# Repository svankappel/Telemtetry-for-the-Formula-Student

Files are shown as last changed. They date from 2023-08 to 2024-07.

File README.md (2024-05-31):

# Telemetry for the Formula Student
## Telemetry
Telemetry is a technology that enables remote measurement and monitoring.This technology is interesting for a race vehicle as it allows live readings from the car's sensors to be monitored directly from the side of the track. With such a system, the data from all the sensors are easily accessible, and the engineers can adjust the car's parameters during the test sessions to increase the car's performance. A telemetry system is also helpful in improving the driver's skills, providing measurements such as GPS, speed, pedal level, steering angle, etc. Direct visualization of measurements also allows problems to be identified before they can cause an accident or damage the car.
## Bachelor's Project
This project aimed to develop and test a telemetry system for the Formula Student car of the HES-SO Valais-Wallis. This thesis deals with the embedded part of the system and the communication with the remote PC. This project was carried out in collaboration with a Business Information Technology student working on the software to display the telemetry system's data.
## MSE PA - Optimizations
This project aimed to enhance the existing system by incorporating additional functionalities
and improving its performance. The objectives of the project are as follows :
- **Addition of a Configurable Filter for the CAN Bus:** The objective of this
section is to implement a filter on the CAN input to allow the passage of other
messages without compromising the performance of the telemetry system.
- **Telemetry System Control via CAN Bus:**
 Currently, recording is initiated and
stopped using a button connected to the system. The objective of this section
is to add the capability to control these functions via the CAN bus.
- **Integration of Time and Date:** The objective of this section is to replace the
current timestamp (relative time since recording started) with absolute time.
- **System Optimization to Enable the Recording of More Data at a Higher
Frequency:** The goal of this section is to push the limits of the number of CAN
messages the system can handle and increase the recording frequency on the SD
card.

The first two points will be implemented on the existing hardware. This is because
the VRT team will need these modifications for the summer 2024 races, and these
optimisations do not require new hardware. For the last two points, the same hardware
is reused, but it is duplicated in order to have one device for the transmission and the
other for the recording.
## Project summary
The telemetry device is connected to the sensors on the car's CAN bus. The
device also includes a GPS module. The CAN bus and GPS module data are
transmitted to the base station via Wi-Fi. The data are also saved on an SD card.
The system is designed to be generic and completely configurable. New sensors
can easily be added to the system by only changing the configuration file.
The device has been successfully developed and tested, and all the objectives
have been reached. The tests showed that the system can transmit data over a
750 meters distance.
## Git Content
The realease branch contains the project's outcome.

- The software folder contains the code of the nRF5340, the busmaster scirpts used for the tests and a configuration file example. The telemetry_system folder contains the code for the system using one device. The telemetry_system_recorder contains the code of the recoridng device for the splitted system and the telemetry_system_transmitter contains the code of the transmitting device for the splitted system. 

- The hardware folder contains the Altium projects, the Bill of material and the Fusion 360 file for the antenna holder.
- The Report folder contains the report of the project. 
- The Miscellaneous folder contains an example of the configuration file, a test and measurement file etc...

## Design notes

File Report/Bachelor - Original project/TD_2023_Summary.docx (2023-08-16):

Telemetry for the Formula Student

| Graduate Sylvestre van Kappel

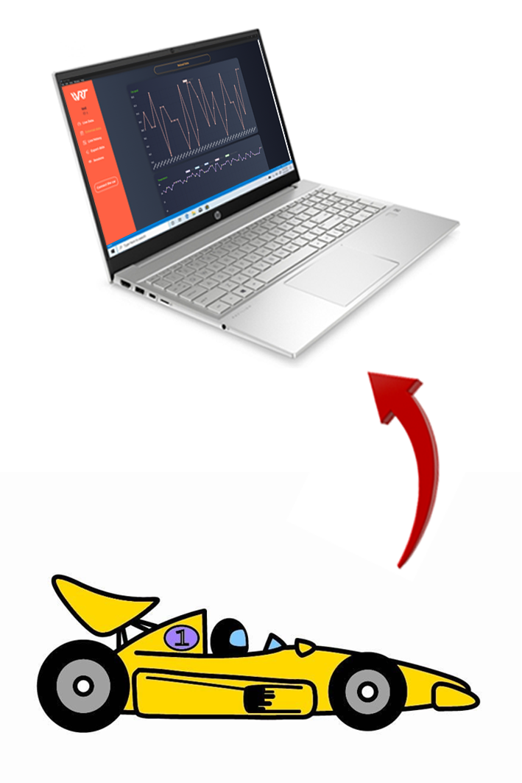
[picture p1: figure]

Bachelor’s Thesis
| 2023 |

Degree programme

Systems Engineering

Field of application

Infotronics

Supervising professor

Medard Rieder

medard.rieder@hes-so.ch

Partner

Valais-Wallis Racing Team

Objectives

This project aims to develop and test a telemetry system for the Formula Student car of the HES-SO Valais-Wallis. This thesis deals with the telemetry system's onboard device and the communication with the PC.

Methods | Experiences | Results

Telemetry is a technology that enables remote measurement and monitoring. This technology is interesting for a race vehicle as it allows live readings from the car's sensors to be monitored directly from the side of the track. With such a system, the data from all the sensors are easily accessible, and the engineers can adjust the car's parameters during the test sessions to increase the car's performance.

The objective of this project is to select the optimum transmission technology and to design and test the hard- and software of the telemetry system’s onboard device.

The telemetry device is connected to the sensors on the car's CAN bus. The device also includes a GPS module. The CAN bus and GPS module data are transmitted to the base station via Wi-Fi. The data are also saved on an SD card. The system is designed to be generic and completely configurable. New sensors can easily be added to the system by only changing the configuration file.

The device has been successfully developed and tested, and all the objectives have been reached. The tests showed that the system can transmit data over a 750 meters distance.

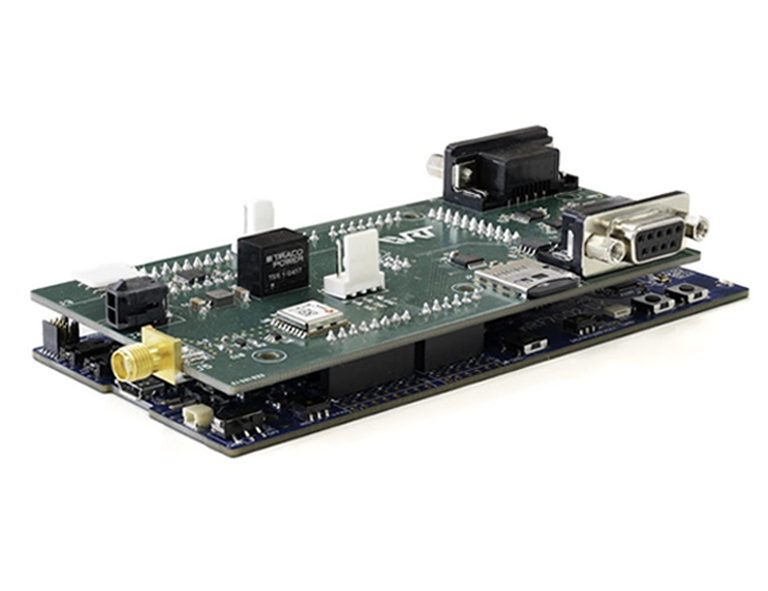
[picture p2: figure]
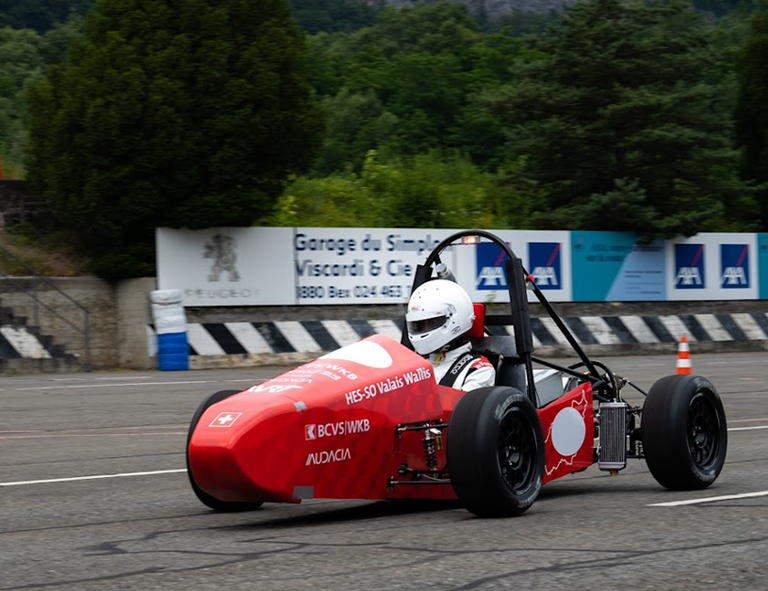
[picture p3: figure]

Valais-Wallis Racing Team’s Car

Telemetry onboard device

HES-SO Valais-Wallis • rue de l’Industrie 23 • 1950 Sion +41 58 606 85 23 • hei@hevs.ch • www.hevs.ch/hei

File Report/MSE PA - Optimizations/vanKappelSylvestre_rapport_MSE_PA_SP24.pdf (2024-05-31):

i

Master of Science HES-SO in Engineering
Av. de Provence 6

# CH-1007 Lausanne Master of Science HES-SO in Engineering

# Major : Computer Science (CS)

# Telemetry for the Formula Student -Optimizations

By

# Sylvestre van Kappel

## Under the supervision of Prof. Medard Rieder HES-SO Valais Wallis

## Sion, HES-SO//Valais-Wallis, 31.05.2024

### Accepted by the HES SO//Master (Switzerland, Lausanne) on the proposal of

### Prof. Medard Rieder, supervisor for the in-depth project

### Sion, 31.05.2024

### Prof. Medard Rieder Supervisor

### Prof. Nabil Abdennadher Program director

# Contents

Contents | iv
List of Figures | vi
List of Tables | vi
List of Listings | vi
1 Introduction | 1
2 System Overview | 5
3 Hardware | 9
4 Software Development | 13
5 Tests | 31
6 Conclusions | 35

iv/41

Contents

7 Appendix | 37
Bibliography | 39
Acronyms | 41

v/41

# List of Figures

1.1 | Valais-Wallis Racing Team’s Car | | 1
1.2 | Current Hardware | | 3
2.1 | System Overview | | 5
2.2 | Telemetry System Display | | 7
3.1 | Bloc Diagram - Current System | | 9
3.2 | Bloc Diagram - New System | | 10
3.3 | New Hardware | | 11
4.1 | Data-Flow Diagram | | 14
4.2 | CAN Button Sequence | | 17
4.3 | GPS Time and Date Data Sequence | | 19
4.4 | CAN Data Sequence | | 21
4.5 | Recording Device Flow Diagram | | 22
4.6 | Transmitting Device Flow Diagram | | 23
4.7 | Booting Sequence | | 24
4.8 | Configuration Transmission | | 25
4.9 | Configuration Reception | | 26
4.10 GPS CAN Frames | | 27
4.11 GPS CAN Frames Transmission | | 28
4.12 GPS CAN Frames Reception | | 29
5.1 | Limits of the system - Base system and upgrades on the existing hardware 32
5.2 | Limits of the system - Base system, upgrades on the existing hardware
| and new hardware | | 33
5.3 | Limits of the system - New System | | 34

# List of Tables

4.1 | CSV File Structure | | 18

vi/41

List of Listings

# List of Listings

4.1 | Configuration of the CAN filter | | 15
4.2 | Configuration of the Record-on-Start | | 16
4.3 | Configuration of the CAN Button | | 16
4.4 | Configuration of the CAN Button | | 17
4.5 | Configuration of the CAN Button | | 27

vii/41

# 1 | Introduction

## 1.1 Formula Student

Formula Student is an international student engineering competition. Teams from all over the world design and build a small-scale Formula-style racing car. During the competitions, the vehicles are judged on static events: Engineering Design, Cost and Manufacturing, Business Presentation, Lap Time Simulation, and Technical Inspection. The vehicle must comply with the rules [1] for the technical inspection. If the car passes the technical assessment, it can participate in the dynamic events: Skidpad, 1 km autocross/sprint, 75 m acceleration, and 22 km endurance.

## 1.2 Valais-Wallis Racing Team

The Valais-Wallis Racing team [2] is the Formula Student team of HES-SO Valais Wallis. It was founded in the spring of 2022 by a group of students. The team’s inaugural car participated in the summer 2023 races, and the telemetry system developed in this thesis will be utilized in the subsequent car for the summer 2024 races. Telemetry was not integrated into the initial car; however, a telemetry system was designed during the summer of 2023.

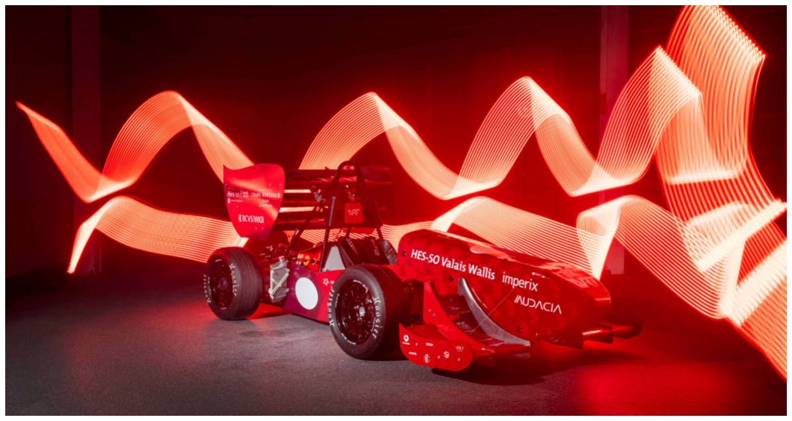
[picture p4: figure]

Figure 1.1: Valais-Wallis Racing Team’s Car

Chapter 1. Introduction

## 1.3 Objectives

Telemetry is a technology that enables remote measurement and monitoring. This technology is interesting for a race vehicle as it allows live readings from the car’s sensors to be monitored directly from the side of the track. With such a system, the data from all the sensors are easily accessible, and the engineers can adjust the car’s parameters during the test sessions to increase the car’s performance. A telemetry system is also helpful in improving the driver’s skills, providing measurements such as GPS, speed, pedal level, steering angle, etc. Direct visualization of measurements also allows problems to be identified before they cause an accident or damage to the car.

This project aims to enhance the existing system by incorporating additional functionalities and improving its performance. The objectives of the project are as follows :

- Addition of a Configurable Filter for the CAN Bus: The objective of this section is to implement a filter on the CAN input to allow the passage of other messages without compromising the performance of the telemetry system.
- Telemetry System Control via CAN Bus: Currently, recording is initiated and stopped using a button connected to the system. The objective of this section is to add the capability to control these functions via the CAN bus.
- Integration of Time and Date: The objective of this section is to replace the current timestamp (relative time since recording started) with absolute time.
- System Optimization to Enable the Recording of More Data at a Higher Frequency: The goal of this section is to push the limits of the number of CAN messages the system can handle and increase the recording frequency on the SD card.

The first two points will be implemented on the existing hardware. This is because the VRT team will need these modifications for the summer 2024 races, and these optimisations do not require new hardware. For the last two points, the same hardware is reused, but it is duplicated in order to have one device for the transmission and the other for the recording.

1.4 Structure of this Report

## 1.4 Structure of this Report

This report is in 4 parts.The first part is a general overview of the system. The second part describes the small hardware modifications that were made, and the third part describes the software optimisations. The last part describes the various tests that were carried out.

## 1.5 Git

All the files referring to the project (codes, altium PCB project ...) and the first release of the project are available on a git repository on the following link :

https://github.com/svankappel/Telemetry-for-the-Formula-Student

## 1.6 Existing Hardware

The following image shows the existing hardware :

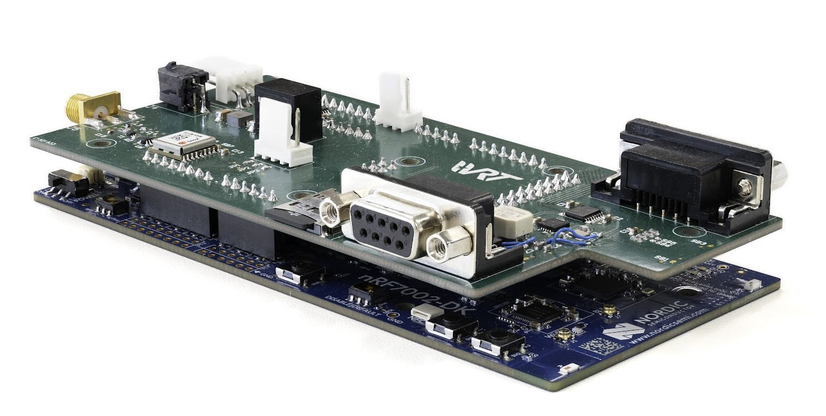
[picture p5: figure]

Figure 1.2: Current Hardware

# 2 | System Overview

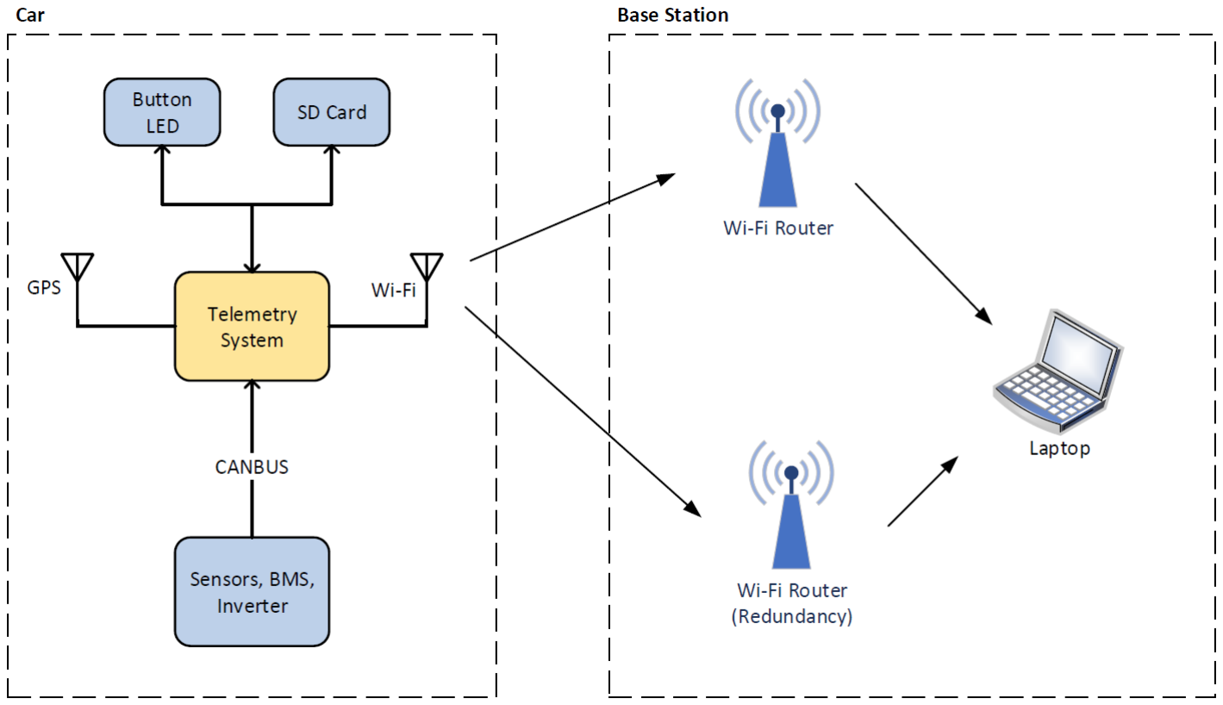
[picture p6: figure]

Figure 2.1: System Overview

This diagram shows the general functioning of the telemetry system. The data coming from the sensors are transmitted by Wi-Fi to the base station.

## 2.1 CAN Bus

The CAN bus is a widely used communication protocol in automotive applications. It was developed in the 1980s by Bosch to allow reliable communication between ECUs in vehicles. The CAN bus protocol is robust and fast. It can handle multiple devices on a single network while maintaining reliability and data integrity.

The CAN bus connects all the different devices of the car that need to communicate. The messages contain various parameters, such as engine speed, pedal status, temperature of the different components, etc. The BMS and the inverter in the actual car include a CAN interface. These two components provide some measurements such as voltage and current of the High Voltage system, power, temperatures, and angular speed. The car will also include more sensors also connected to the CAN bus.

The telemetry system is connected to the CAN bus and retransmits the data from the sensors.

Chapter 2. System Overview

## 2.2 SD Card

The system includes an SD card. The SD card has two functions.

The first function is to hold a configuration file. It is a JSON file that contains all the information the system needs to work correctly. The configuration file contains the settings for every sensor. A new sensor can be easily added by putting its CAN settings in the configuration file.

The second function is to register the measurements made by the sensors. When the button is pressed, the recording is activated, and the LED on the button blinks. When the button is pressed again, the recording is stopped. The data on the SD card provide a backup in case the transmission is interrupted. The data from all sensors are recorded at a high frequency. These data are saved in CSV files.

## 2.3 Wi-Fi Transmission

The Wi-Fi transmission includes an optional redundancy. When it is activated, the system tries to connect to the first router. If it cannot connect, it tries with the second router. It then retries with the first if the second is unreachable, etc.

The settings of the Wi-Fi connection (SSID, password) are set in the configuration file. The system can use any standard Wi-Fi router. It employs the WPA2 security protocol but can be easily migrated to WPA3.

The data of only a selected number of sensors shall be live transmitted to the base station. A boolean field in the configuration file indicates whether the data of each sensor shall be transmitted or not. The transmission frequency is also defined in the configuration file. The defined frequency is lower than the recording frequency.

## 2.4 GPS

The telemetry device includes a GPS. It provides the GPS coordinates and the speed of the car. As for the sensors, the data are saved in the CSV files and can also be sent by the Wi-Fi transmission.

2.5 Front End

## 2.5 Front End

The software on the base station’s PC displays the data sent by the telemetry device. The data saved on the SD card can also be loaded on the software. This software was developed by a student from the Business Information Technology program.

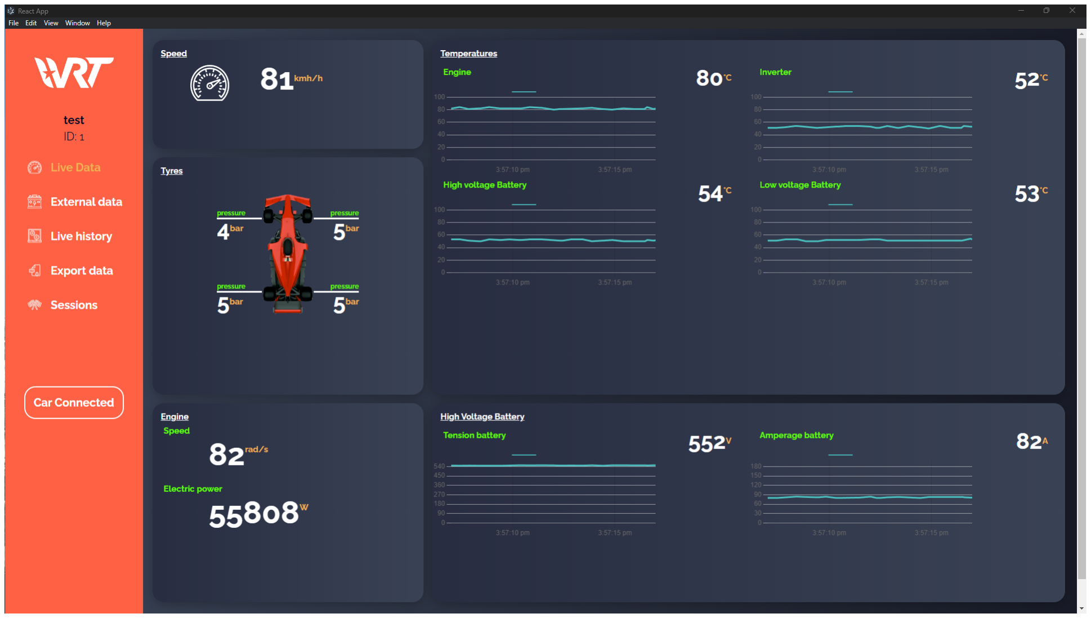
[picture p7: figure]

Figure 2.2: Telemetry System Display

The software can be downloaded at the following link :

https://vrt.simonbeaud.ch/

## 2.6 Optimizations

The optimizations do not alter the general system overview. The system continues to function in the same manner. The CAN filter and CAN button functionalities merely introduce some configuration adjustments in the configuration file. The inclusion of time and date provides additional data in the CSV recording file.

# 3 | Hardware

## 3.1 Existing System

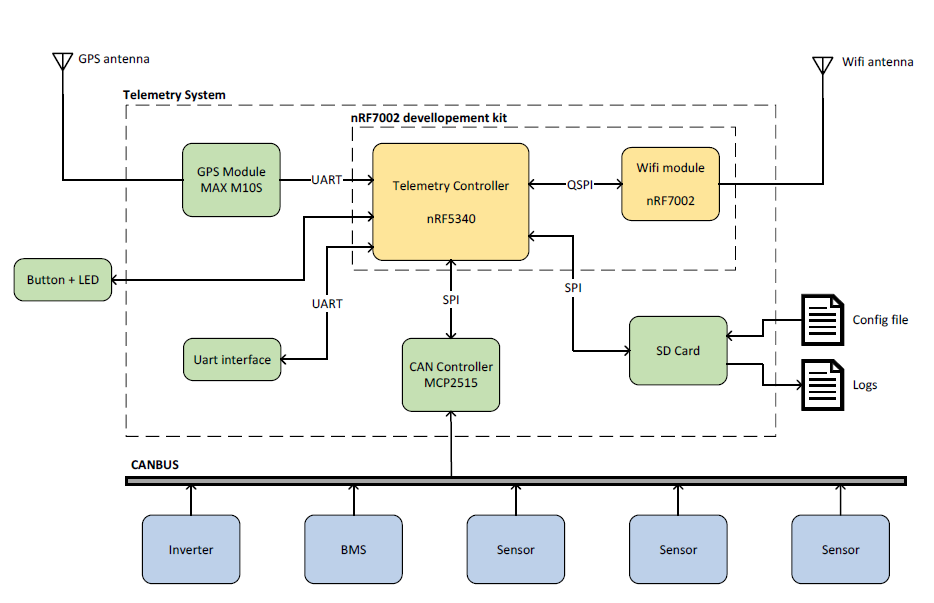
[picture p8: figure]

Figure 3.1: Bloc Diagram - Current System

This diagram shows the general architecture of the telemetry system’s onboard device. The CAN Filter and the CAN button are implemented on this version on the hardware (and also on the new version).

The main controller (nRF5340) is the central element of the system.

The CAN controller is connected to the nRF5340 via an SPI bus. On the other side, it is connected to the CAN bus to communicate with the BMS, the inverter, and all the sensors.

Another peripheral is the GPS module. It is connected to the nRF5340 via a UART communication. The GPS module uses an external antenna because it needs to be pointed to the sky, and the telemetry system will be placed in a case in the car.

The microSD card is connected to the nRF5340 via an SPI bus. The microSD card serves to store the measurements of the telemetry system. The memory card also holds a configuration file.

The nRF7002 chip handles Wi-Fi communication. It is connected to the nRF5340 via a QSPI bus. As for the GPS module, the Wi-Fi module uses an external antenna to improve the transmission.

Chapter 3. Hardware

The system also includes a button with an intern LED. The button permits to start and stop the recording of the logs, and the LED indicates the system’s status. The button will be placed on the dashboard of the car.

The last peripheral is a UART interface. The telemetry system does not use it. It is just there for future system improvements (to connect an onboard computer, for example).

## 3.2 New System

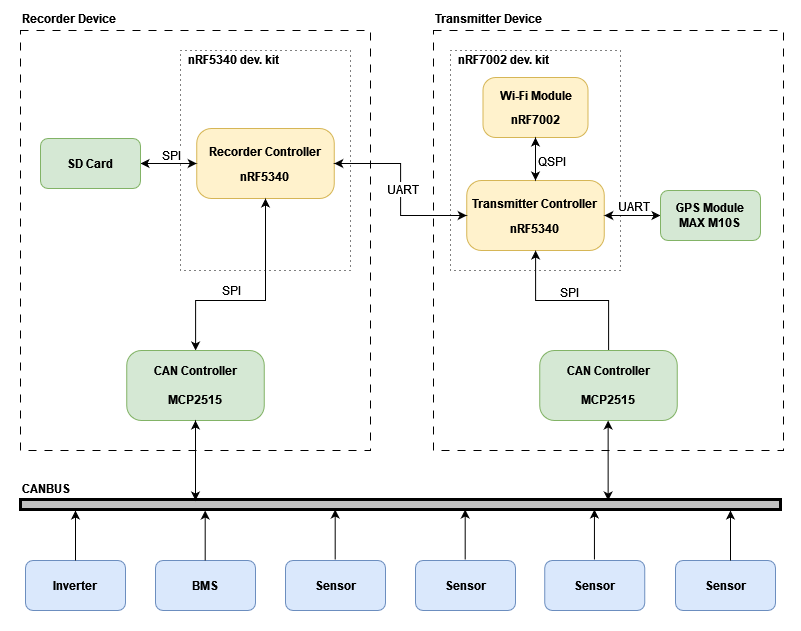
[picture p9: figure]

Figure 3.2: Bloc Diagram - New System

The new hardware is identical to the existing version, but the system has been duplicated, with only the components required by each respective device being mounted on the PCB. For the recording device, the nRF7002DK was replaced by a nRF5340DK as it does not require Wi-Fi. The two devices are connected together via a UART bus and they both have their own CAN Controller.

3.2 New System

The following image shows the new hardware:

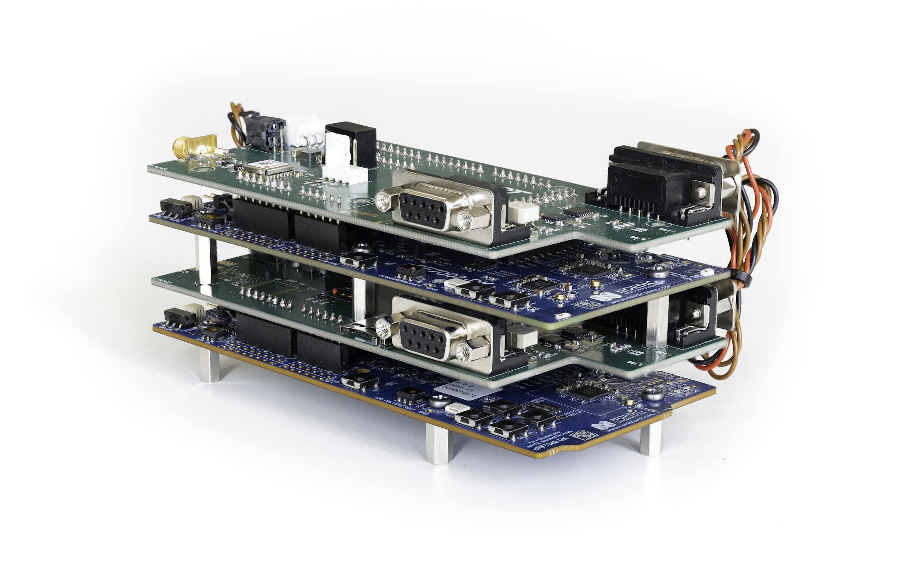
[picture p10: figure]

Figure 3.3: New Hardware

# 4 | Software Development

## 4.1 Existing System Design

The software implemented on the nRF5340 uses the Zephyr RTOS. Zephyr RTOS is a compact operating system designed for devices with limited resources. Nordic’s advanced hardware, renowned for its performance and efficiency, fits absolutely with Zephyr’s lightweight and modular design.

The software is implemented on the application processor of the nRF5340. It was developed with the nRF Connect SDK v2.3.0.

The software implements the following tasks working in parallel:

- Wi-Fi Station
- UDP Client
- Data Sender
- Data Logger
- GPS Controller
- CAN Controller
- Button Manager
- LED Controller

The main function starts the Button Manager and the LED Controller first. Then the configuration file is read, and all the other tasks are started if the reading of the file is successful.

The design includes two buffers. The first is the sensor buffer. It contains the value and the configuration of every sensor present in the configuration file. The CAN Controller writes the values received by the sensors on this buffer. The second buffer is the GPS buffer. It works like the sensor buffer but takes its data from the GPS Controller.

The Data Sender periodically reads the sensor and GPS buffers and creates a JSON message containing the sensor and GPS values configured to be sent on the live transmission. Then it puts it in the UDP queue.

The UDP Client reads the UDP queue and sends the messages to the base station via the Wi-Fi using a UDP socket. The UDP protocol was chosen because it is faster than TCP, and the transmission does not need to be 100% reliable because the messages are periodically re-transmitted. Consequently, it is not a problem if sometimes a transmission contains an error.

When the button is pressed, the Data Logger creates a new CSV file on the SD card. It then periodically reads the sensor and GPS buffers and writes a new line on the CSV file with the read values. When the button is pressed again, the recording is stopped. The LED on the button is blinking when the Data Logger is recording.

The Wi-Fi Station manages the Wi-Fi connection.

Chapter 4. Software Development

The following diagram shows the system’s general architecture:

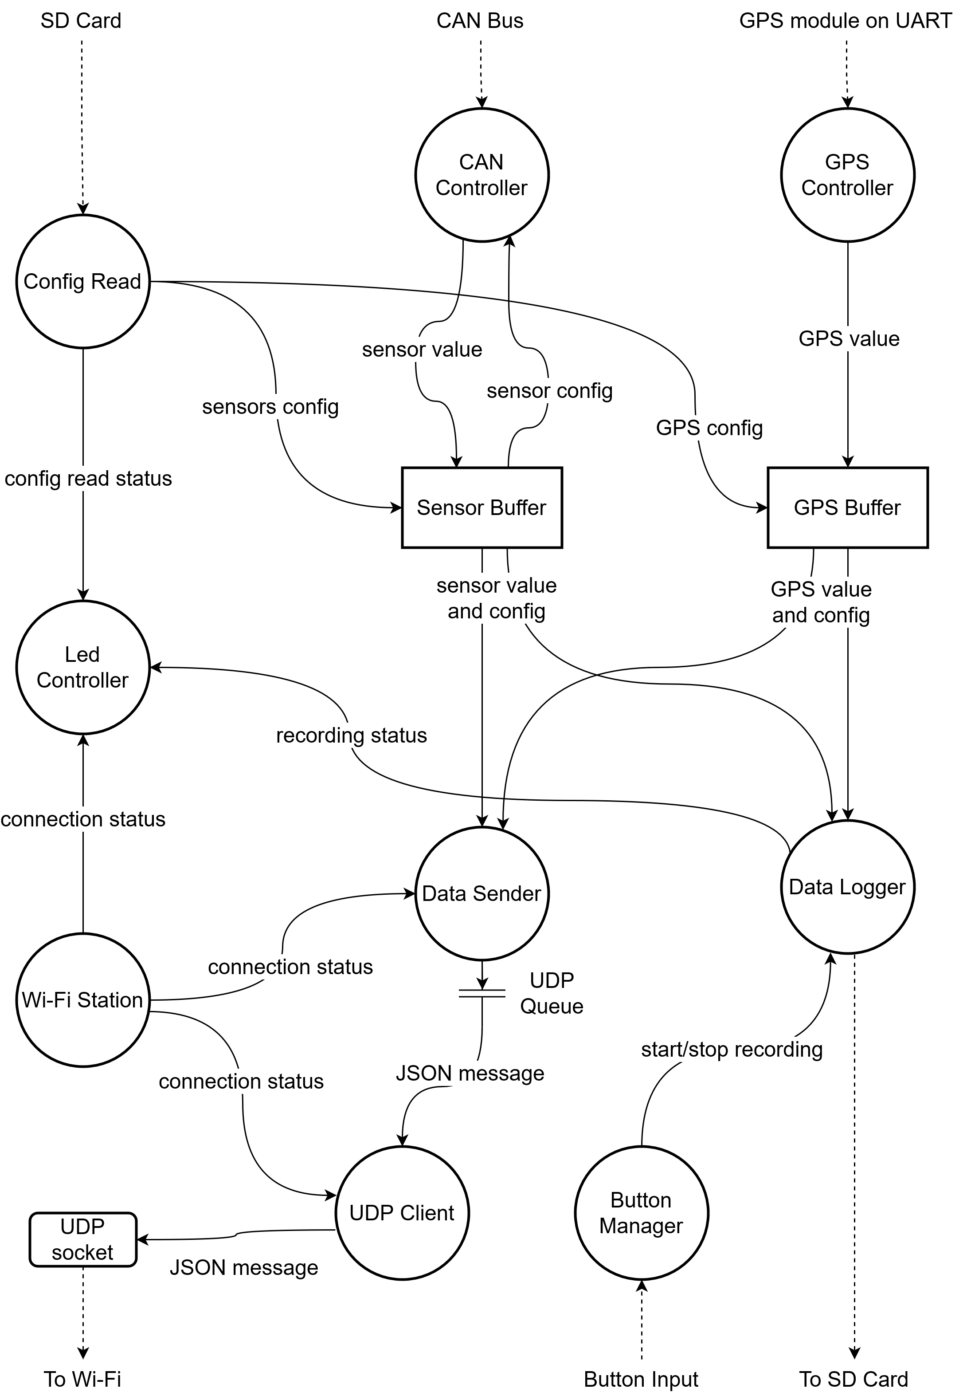
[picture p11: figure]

Figure 4.1: Data-Flow Diagram

4.2 CAN Filter

## 4.2 CAN Filter

The first optimization added to the system is the CAN filter. The Zephyr CANBUS API
[3] allows a CAN filter to be set. Messages not intended for the telemetry system are also sent over the CANBUS. The existing system also processes these messages, reads them, and then ignores them. This takes some time and affects the performance of the system. Tests have shown that the system cannot handle more than 200 messages per second to function reliably. By adding a CAN filter, a range can be defined, and message IDs that are not in the range will be ignored without affecting the performance of the system.

The CAN filter is set during the initialization of the CAN device in the CAN controller component. It takes two arguments: an ID and a mask. The filter works as follows:

A message is accepted if the following condition is true :

(filter ID & mask) == (message CAN ID & mask)

For instance, with the following configuration, only messages with a CAN ID in the specified range will be considered:

ID = 0xAA = 0b10101010

Mask = 0xF0 = 0b11110000

Messages taken into consideration are 0xA0, 0xA1, ..., 0xAF.

This allows creating ranges of CAN IDs that are designated for the telemetry system.

As the system must be configurable, the ID and mask have been added to the configuration file of the system. The configuration file is read when the program starts, and the values are stored in a structure that is then accessed by all the components of the system.

"CANFilter":
{
"id":"0x0",
"mask":"0x0"
}

Listing 4.1: Configuration of the CAN filter

Chapter 4. Software Development

## 4.3 CAN Button

On the existing system, the only way to start and stop the recording is to push the physical button. An LED on the button indicates if the system is currently recording.

The goal of this part is to start and stop the recording with a message on the CAN bus. The telemetry system must also emit a message on the CANBUS to indicate if it is currently recording or not, to replace the LED. This allows the button and the LED to be connected via the CANBUS, avoiding additional wiring. With this solution, the telemetry system will also be controllable by the on-board computer. The system must also include an option to automatically start the recording on boot.

To achieve this, several configurations have been added to the configuration file. The first is a boolean to enable recording on startup:

"RecordOnStart":false,

Listing 4.2: Configuration of the Record-on-Start

Next, there are the button configurations. There are two configurations: one to start and one to stop the recording. These configurations require a CAN ID, the length of the message, the index of the byte that contains the information in the message, the match value (the value the message must correspond to in order to start/stop the recording), and finally a mask for this match, which allows using only a single bit so the same byte can transmit other information:

"CANButton":
{
"StartLog":
{
"CanID":"0x010",
"dlc":8,
"index":7,
"match":"0x01",
"mask":"0x01"
},
"StopLog":
{
"CanID":"0x010",
"dlc":8,
"index":7,
"match":"0x00",
"mask":"0x01"
}
},

Listing 4.3: Configuration of the CAN Button

4.3 CAN Button

There is also a configuration for the "LED". A message indicates if the device is recording. For this, the system will emit a 0x01 when it is recording and a 0x00 when it is not recording, on the CAN ID specified in the configuration:

"CANLed":
{
"CanID":"0x11"
},

Listing 4.4: Configuration of the CAN Button

To send the LED message, an event was added to the Data Logger component. When the recording successfully starts, a function is called in the CAN Controller. A callback method with a function pointer is used to pass the functions to the Data Logger. In the CAN Controller, the message is formed with the CAN ID configured in the configuration file, and the message is sent.

For the CAN Button, when a message arrives on the CAN, it is put in a queue that the CAN Controller component reads. If the CAN ID matches the ID of the start or stop message, the same function that is called by the button controller is invoked. This creates a work item [4] that then calls the start or stop function in the Data Logger component.

The following diagram shows the sequence of the function called when a start message arrives on the CANBUS :

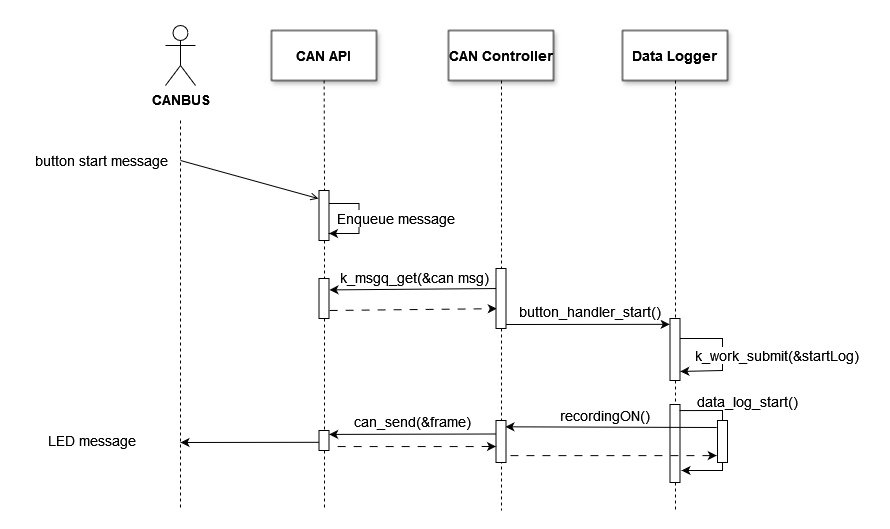
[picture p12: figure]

Figure 4.2: CAN Button Sequence

Chapter 4. Software Development

## 4.4 Time and Date

The aim of this chapter is to add a time and a date to the recordings. For this, the system needs to know the current time. There are three options to achieve this:

- Remote PC: The first option is to request the time from the remote PC via Wi-Fi communication. The issue with this approach is that the system may be used without Wi-Fi, in which case it would not be able to provide the time.
- Real-Time Clock (RTC): An RTC is an integrated circuit that provides the time. It must be powered by a small battery to retain the time when the system is powered off. The drawback is that hardware modifications would be necessary, and there was not enough time for such modifications in this project.
- GPS: The system’s GPS module also provides the time and date. The only problem is that the GPS signal can be weak indoors. To ensure this would not cause problems, tests were conducted in the Valais-Wallis Racing Team’s workshop. The results indicated that the GPS signal inside the workshop was strong enough to obtain the time and position as quickly as outside.

The GPS module works with the NMEA protocol [5]. Frames are transmitted to the nRF5340 via a UART bus. The frame that contains the date and time is the RMC frame. The GPS module sends data every second. On reception, it triggers an interrupt. During the interrupt routine, the message is pushed to a queue. The GPS Controller component reads from the queue, parses the NMEA frame, and writes the time and date data to the GPS buffer. When a recording is started in the Datalogger component, the time and date are read on the GPS buffer and written to the first line of the CSV file.

The CSV file uses the following structure:

Date: | 31-05-2024 | Time: | 09:45:12
Timestamp [ms] | Sensor1 | Sensor2 | Sensor3 | Sensor4
50 | 10 | 34567 | 156 | 332
100 | 12 | 30678 | 876 | 333
150 | 15 | 22344 | 459 | 335

Table 4.1: CSV File Structure

4.4 Time and Date

The following diagram show the sequence of the GPS data from the GPS module to the CSV file:

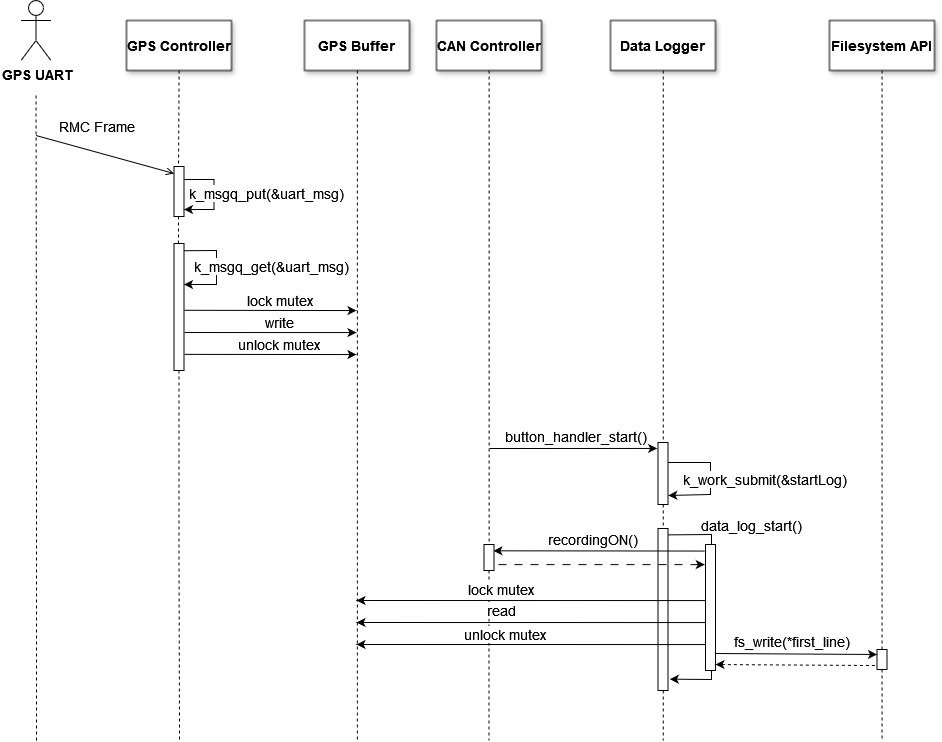
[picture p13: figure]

Figure 4.3: GPS Time and Date Data Sequence

Chapter 4. Software Development

## 4.5 System Optimization

The aim of this chapter is to optimise the performance of the system. Currently the system can process 200 messages per second on the CAN bus. If the message rate exceeds this limit, data loss can occur because the processor does not have enough time to process each message and write the data to the SD card. In addition, the processor must simultaneously handle Wi-Fi connectivity, data transfer and GPS tasks. These parallel operations fully utilise the processor’s capacity, resulting in incoming CAN messages arriving faster than they can be processed. To prevent data loss, the CAN controller uses a FIFO buffer to temporarily store messages until they are processed. However, if the buffer fills up faster than it can be emptied, any further incoming data will be lost once the buffer is full.

It’s important to note that the 200 messages per second limit may vary depending on other system configurations, such as the frequency of writing to the SD card and the amount of data written to the SD card. These factors have a significant impact on overall system performance and its ability to handle incoming messages without data loss.

There are two ways to optimise the performance of the system. The first is to reduce the time taken by tasks that are frequently called, and the second is to reduce the number of tasks that are executed by the processor by splitting the system between two processors. The split was made so that one processor was dedicated to recording on the SD card and the other to transferring the data.

4.5.1 Optimization on the existing device The existing system is already relatively straightforward, with limited opportunities for optimization. The only significant non-essential time-consuming process is the periodic synchronisation of the SD card [6]. When the function to write to the SD card is called, the data is not necessarily written directly to the SD card. Instead, the data is initially written to a cache memory, which is then copied to the SD card when a significant amount of data has accumulated. In the current system, the cache is periodically flushed in order to save data in the event that the user fails to stop recording before shutting down the system. However, in the new car, the recording is controlled by the car’s embedded computer rather than a human operator. Consequently, this situation will not occur, and the periodic synchronization can be eliminated.

4.5 System Optimization

The data is written to the sd card with the following sequence:

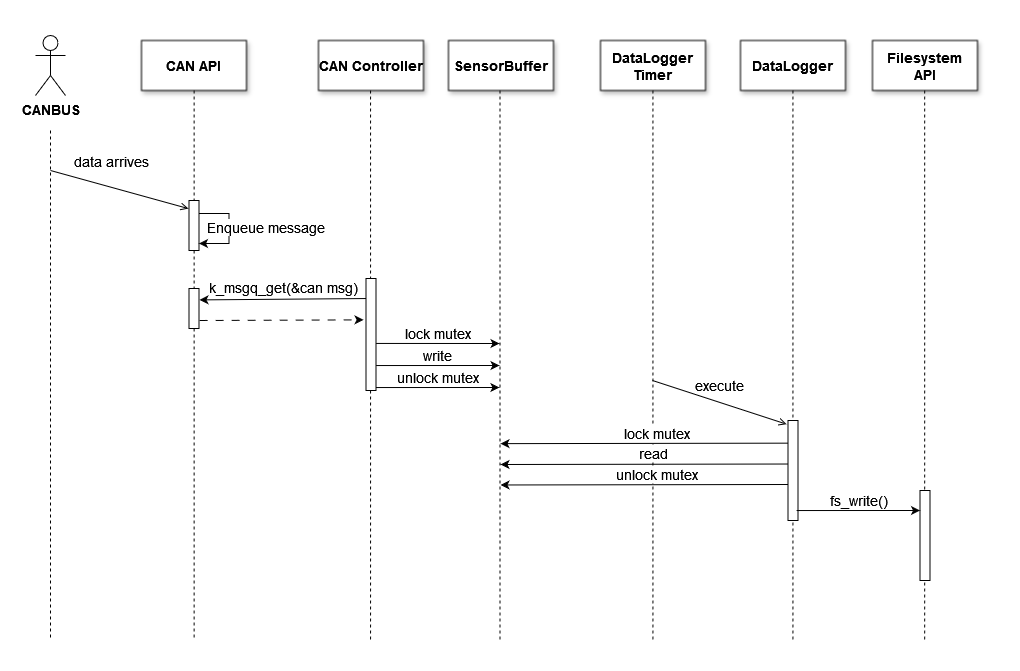
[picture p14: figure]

Figure 4.4: CAN Data Sequence

4.5.2 | Optimization on the new hardware
| To improve the optimization, the device was duplicated, with one dedicated to trans- mitting and the other to recording. This allows two factors of improvement: first, each processor has fewer tasks to manage, and second, the processor dedicated to recording can run at 128 MHz instead of 64 MHz, since Wi-Fi requires the processor to run at 64 MHz in the SDK version used during development.
| Dividing the system into two units makes it possible to eliminate certain tasks on each unit. The GPS is kept only on the transmission device, since the priority is to optimize the recording function. The SD card is kept only on the recording device. Consequently, GPS data must be transferred to the recording device and the configuration file must be transferred to the transmission device.

Chapter 4. Software Development

The following data flow diagram shows the general architecture of the recording device:

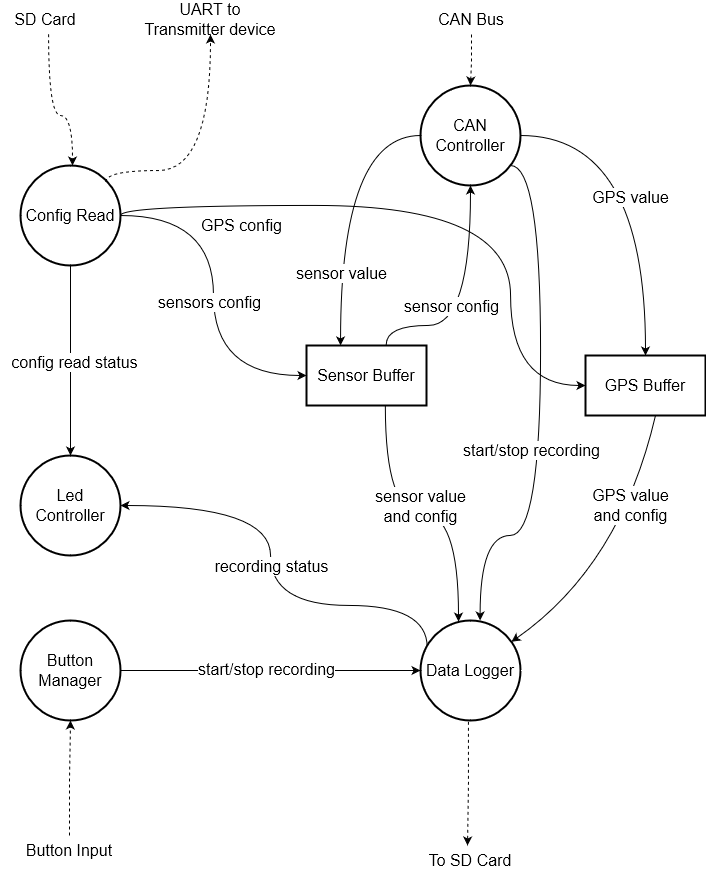
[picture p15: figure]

Figure 4.5: Recording Device Flow Diagram

4.5 System Optimization

The following data flow diagram shows the general architecture of the transmitting device:

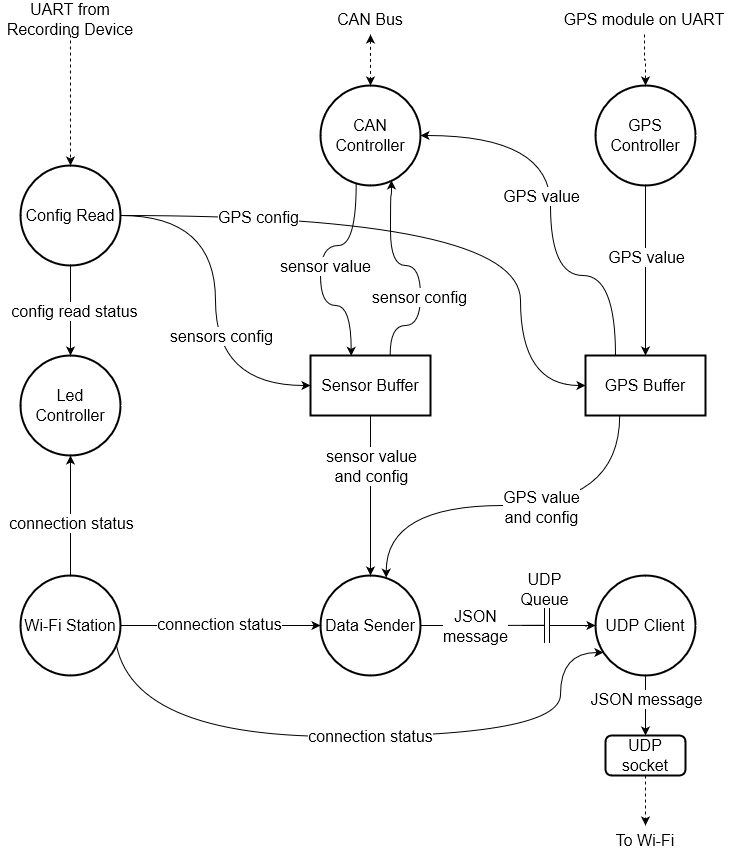
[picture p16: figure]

Figure 4.6: Transmitting Device Flow Diagram

Chapter 4. Software Development

4.5.3 Configuration File Transfer The configuration file is transferred from the recording device, which has the SD card, to the transmitting device using a UART bus. Because the file is 8 KB, this transfer is more complex than the control of the GPS module (e.g., GPS, as described in the original device report), which is only a few bytes. The transmission uses the Zephyr UART [7] with the interrupt-driven API. The UART device is configured to operate at a baud rate of 115200. At this speed, an 8 KB configuration file is transferred in approximately one second. When the system powers up, the LED and button controllers are initialized first on both devices. Next, the transmitter device pauses and waits for the configuration. On the recording device, the configuration file is read and parsed before being sent via UART. After the configuration is sent, all other components of the recording device are initialized and started. Once the transmitting device receives the configuration, it parses the file and then starts the other components. The following diagram shows the booting sequence on both devices :

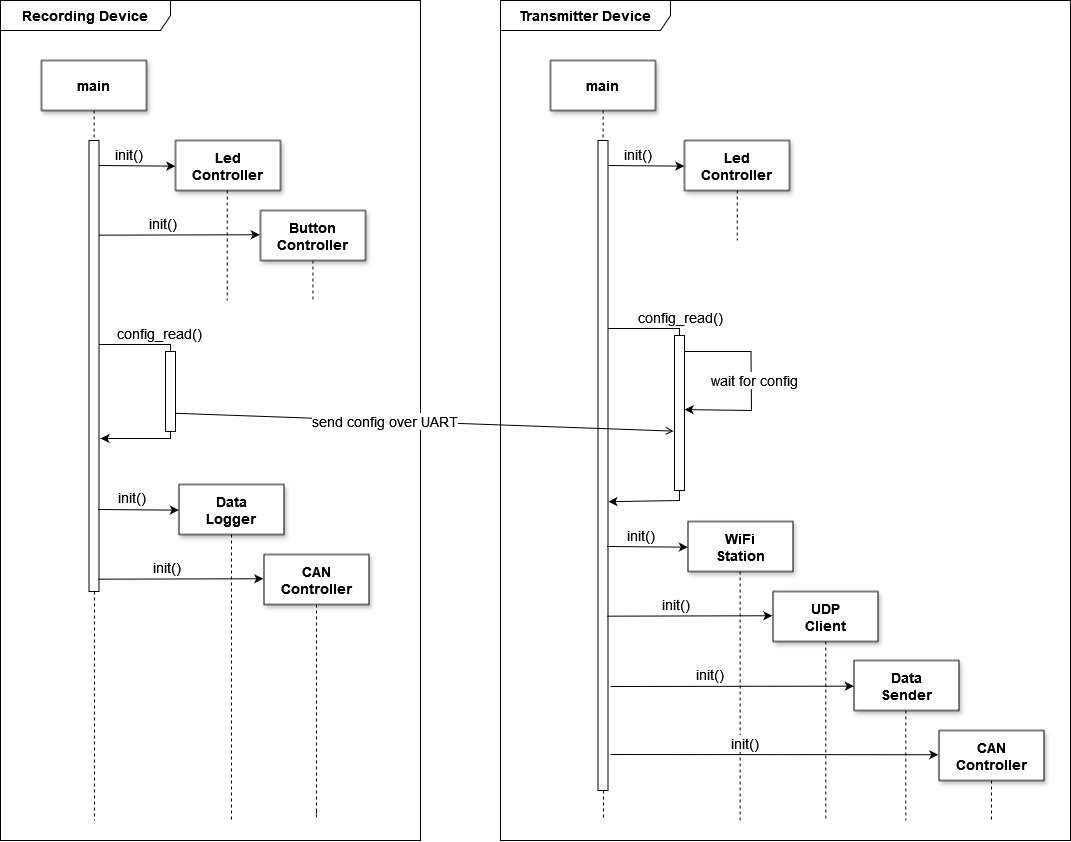
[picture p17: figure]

Figure 4.7: Booting Sequence

For the transmission of the configuration file, the code works with small temporary buffers and the bytes are copied using the memcpy operation, which copies multiple bytes simultaneously. This is important because bytes need to be stored quickly as they arrive. Copying bytes one at a time using the polling API is insufficient because the bytes arrive faster than they can be stored, resulting in data loss.

4.5 System Optimization

For the send portion, when the UART interrupt is enabled, an interruption is triggered when the device is ready to send data. During the interrupt routine, the system attempts to send a 512-byte chunk. The send function returns the number of bytes actually sent; if less than 512 bytes are sent, the system continues to send the remaining bytes in a loop. When the chunk is completely sent, the system waits for the next interruption to send the next chunk. The buffer containing the configuration file is slightly larger than the file itself and is initialized with "\0" to ensure that a terminating character is automatically added. After the entire file has been sent, the 0x14 symbol indicates that the transfer is complete. Once the file is sent, the UART device interruption is disabled as it is no longer needed.

The following activity diagram shows how the transmission works:

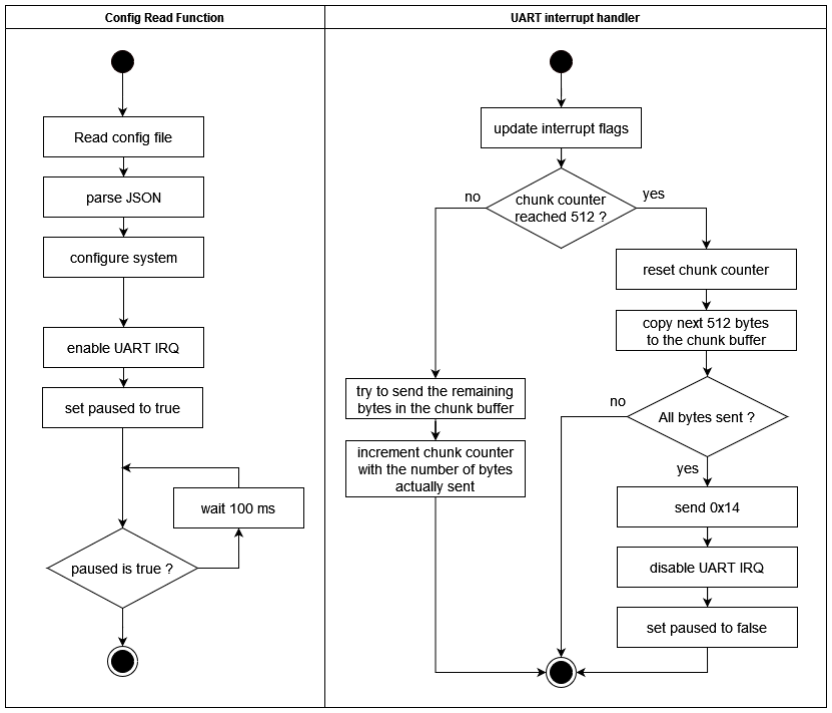
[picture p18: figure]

Figure 4.8: Configuration Transmission

A similar process applies to the receiving part. An interrupt is generated when new bytes arrive in the UART receiver. During the interruption, the system attempts to read a 64-byte chunk. The read function returns the number of bytes read, and the system copies those bytes into the buffer containing the complete configuration file. The system then waits for the next interrupt to continue copying bytes from where it last stopped. When the terminator (0x14) is detected, the UART device interrupt is disabled because it is no longer needed.

Chapter 4. Software Development

The following activity diagram shows how the reception works:

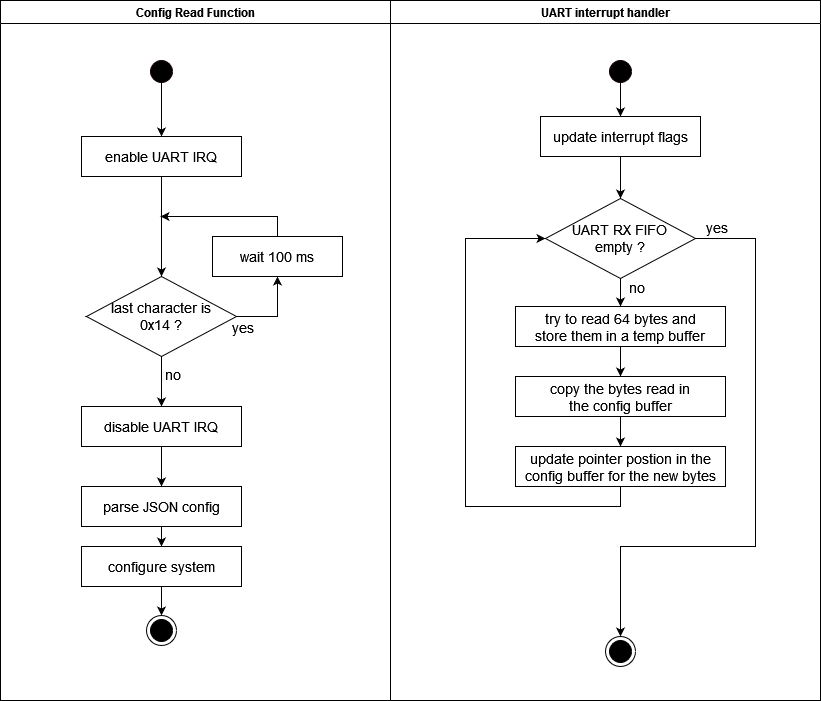
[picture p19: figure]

Figure 4.9: Configuration Reception

4.5 System Optimization

4.5.4 | GPS data transfer
| The GPS data is parsed and small calculations (e.g., unit conversions, as detailed in the original device report) are performed on the transmission device. The data is then transmitted over the CAN bus to the recording device. On the recording device, the data is placed in the GPS buffer, mimicking the input from the GPS module. Using the CAN bus allows the same thread to handle receiving data from the GPS and other sensors, improving performance.
| As data is transferred over the CAN bus, CAN IDs must be assigned to the system. To ensure the system is configurable, a field was added to the GPS section of the configuration file. Three IDs need to be assigned: the first for a message containing the longitude, the second for the latitude, and the third for a message that includes the fix information, vehicle speed, time, and date.
| The configuration file section simply contains three fields for the CAN IDs:
| "CanIDs": { "Lat":"0x05", "Long":"0x06", "TimeFixSpeed":"0x07" }
| Listing 4.5: Configuration of the CAN Button

The following figure illustrates how the data is stored in the CAN frame:

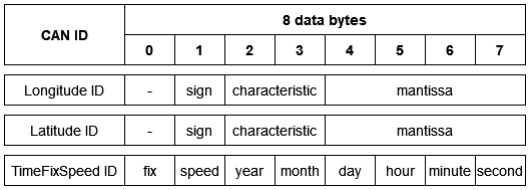
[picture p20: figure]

Figure 4.10: GPS CAN Frames

Chapter 4. Software Development

On the existing system, GPS data is received by the GPS Controller component. The data is then written to the GPS Buffer. To send the data to the recording device, a new timer was added with a period fixed at 1 second, matching the GPS module’s data transmission rate. During the timer interruption, a work item [4] is submitted to avoid blocking other processes during the interruption. In the work handler, CAN frames are created with the values currently present in the GPS buffer and are sent using the Zephyr CAN API [3].

The following sequence diagram shows how the GPS data are sent over the CAN bus:

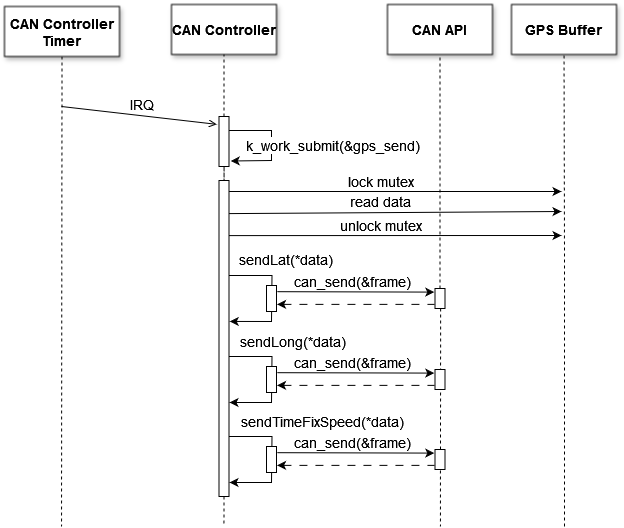
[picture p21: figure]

Figure 4.11: GPS CAN Frames Transmission

On the recording device, the reception of GPS data works similarly to the other data transported on the CANBUS. The incoming frames are stored in a queue by the CAN Zephyr API. The CAN Controller component reads the queue and processes the frames. If the CAN ID corresponds to GPS data, the data is extracted from the frame and written to the GPS buffer.

4.5 System Optimization

The following sequence diagram shows how the GPS data is received from the CAN bus:

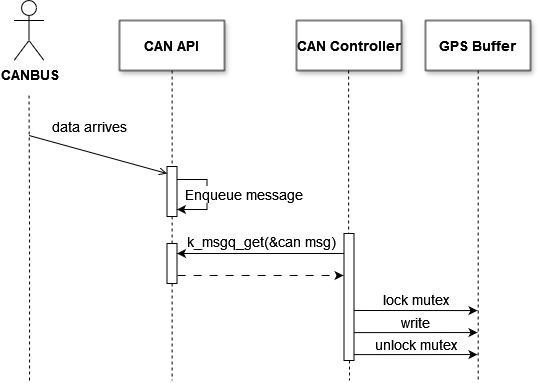
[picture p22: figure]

Figure 4.12: GPS CAN Frames Reception

At this point, the GPS buffers of both devices are synchronized. The operations involving the GPS data, such as reading from the module via UART, writing to the SD card, and transmitting to the remote PC, were copied from the existing system.

The results of the optimizations are measured and commented in the Tests chapter.

# 5 | Tests

The tests aim to measure the impact of the optimizations on performance and to define the system’s operating point. Since the system is highly configurable, performance varies significantly depending on the configuration. Adding more sensors, CAN frames, etc., will affect performance. The tests were conducted on a configuration similar to the one that will be used in the car.

The test variables are the message frequency on the CAN bus and the recording frequency on the SD card. The results show the maximum values for these two parameters.

The other parameters are fixed for all the tests :

Wi-Fi transmission : enabled
GPS : Active with fix
Log recording : enabled
Number of sensors configured : 22
Number of different CAN messages destined to the telemetry system : 8 Number of different CAN messages destined to the telemetry system : 4

The CAN bus is working at 500 KBits/sec. A CAN message is 125 bits long on average, which means the CAN bus is saturated at 4000 messages per second. However, these tests targets to characterize the telemetry system’s limits and not the CAN bus limit, so to avoid problem with the CAN bus saturation, the CAN message rate was limited to 3400 messages per second, which correspond to an 85% usage of the CAN bus.

The recording frequency was tested up to 1000 records per second because the system is not designed to operate at higher frequencies. Additionally, recording logs at higher frequencies would be impractical, as it would require sending messages on the CAN bus at 1 kHz, quickly saturating the bus.

The tests were performed by gradually increasing the CAN bus message rate and recording rate until the system failed. The last sets of working parameters were retained to characterize the system’s limits. The CAN bus message rate included only the messages destined for the telemetry system. During the tests—except for the base system tests that did not include the CAN filter—additional messages not destined for the telemetry system were sent on the CAN bus, totaling 3400 messages per second, to test if the CAN filter was working well. A test was considered passed if the system operated for 30 minutes without the CAN buffer overflowing.

Chapter 5. Tests

The following chart shows the results for the existing system and for the upgrades made on the existing hardware :

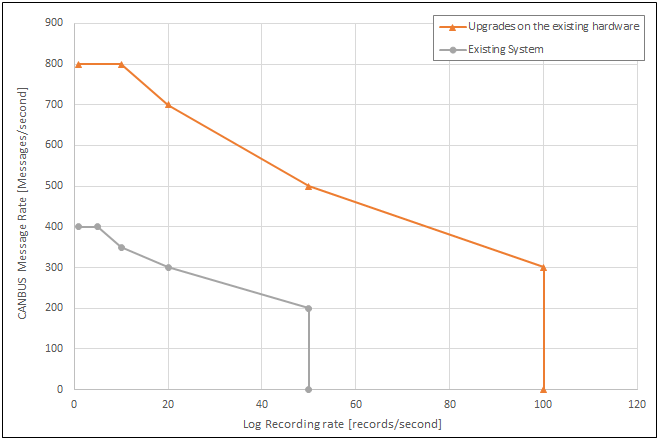
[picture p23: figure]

Figure 5.1: Limits of the system - Base system and upgrades on the existing hardware

The results show that the initial software upgrades significantly increase the system’s performance. This improvement is primarily due to the elimination of the periodic cache flush. Additionally, the tests demonstrate that messages not destined for the telemetry system do not interfere with its operation.

The following chart adds the limit of the new system working on the new hardware:

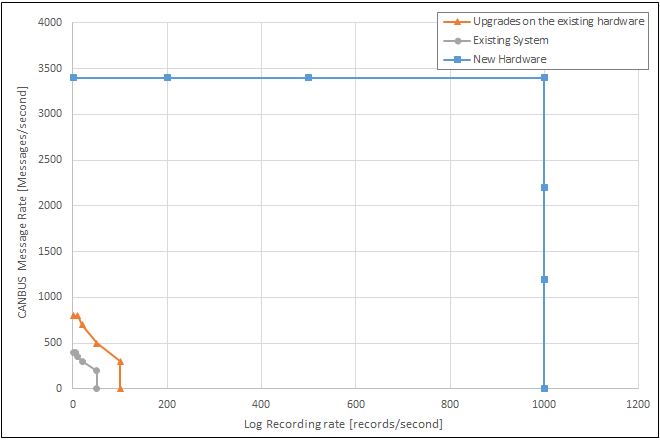
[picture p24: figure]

Figure 5.2: Limits of the system - Base system, upgrades on the existing hardware and new hardware

The performance rise is mind blowing compared to the system working on a single device. The performance is not anymore restricted by the telemetry system but by the CAN bus. The performance gain can be explained by multiple factors.

First, splitting the device in two reduced the number of tasks running in parallel on each device, providing more CPU time for the CAN Controller and Data Logger tasks. Additionally, it reduced the number of context switches, and decreased concurrency on shared resources, thus minimizing the time a thread is blocked by a mutex, preventing it from performing its work.

Another benefit of splitting the system was that it allowed the recording device to be clocked at 128 MHz instead of 64 MHz. The existing system operated at 64 MHz because the Wi-Fi functionality did not work at 128 MHz with the version of the SDK and Zephyr used during its development.

It’s also important to understand that the system operating on a single device is not incapable of working beyond its limits. However, it becomes unstable, and the CAN Buffer occasionally overflows, leading to data loss. This explains why even a modest increase in CPU time resulted in astonishing improvements.

The last test illustrates the system’s performance when the CAN filter is not configured correctly. In this test, messages not intended for the telemetry system are not filtered. Instead, all messages are placed in the CAN buffer and must be analyzed. Similar

Chapter 5. Tests

to previous tests, the CAN bus message rate only reflects the number of messages intended for the telemetry system. The total message rate is 3400 messages per second.


Figure 5.3: Limits of the system - New System

The results indicate that when there are messages not intended for the telemetry system, the system’s performance decreases compared to the performance with the same parameters but with messages destined for the telemetry system. This might seem counter-intuitive, but it is explained by how the messages are analyzed in the CAN Controller. When a CAN message is parsed, a loop iterates through the sensor buffer to determine where the data should be placed. Once found, the loop breaks, and the next message can be processed. However, if the message is not intended for the telemetry system, the loop traverses the entire sensor buffer unnecessarily. As a result, a message not intended for the telemetry system takes twice the average time to analyze compared to a message intended for the telemetry system.

In summary, the tests have shown significant improvements in performance. However, it’s important to interpret the absolute results with caution, as system configuration has a significant impact on performance. Nevertheless, the tests were carried out in a configuration as close as possible to real-world conditions.

# 6 | Conclusions

## 6.1 Project summary

The aim of this project was to improve the existing telemetry system used by the Valais-Wallis Racing Team (VRT) for their Formula Student car. The project began by adding a configurable filter to the CAN bus to allow selective message passing without degrading system performance. The second objective was to enable system control via the CAN bus, replacing the manual push-button control. To integrate time and date, the existing relative timestamp system was extended to include absolute time and date. The final objective was to globally optimize the system to handle a higher frequency of data acquisition. This was achieved by splitting the system into two devices: one for data transmission and one for data recording, reducing the processing load on each device and improving overall performance.

## 6.2 Comparison with the initial objectives

All the initial objectives were successfully met. The addition of the CAN bus filter and CAN-based control improved the flexibility and usability of the telemetry system. The integration of time and date gives more detail to the recordings. The most significant improvement came from system optimization, where splitting the system into two units not only met but exceeded performance expectations. This configuration allowed the system to handle a higher frequency of CAN messages and data logging, demonstrating a significant increase in performance over the original single unit setup.

## 6.3 Encountered difficulties

One of the biggest challenges during the project was splitting the system into two units. The complex part was transferring the configuration file between the units, which took more time than expected. The configuration file, stored on an SD card on the recording unit, had to be transferred to the transmitting unit via a UART bus. This process, which was finally successfully implemented, required meticulous handling to ensure data integrity and system synchronisation, adding unexpected delays to the project schedule.

Chapter 6. Conclusions

## 6.4 Future perspectives

Looking ahead, there are two primary areas for further enhancement:

- Improvement of Time and Date Handling
To enhance the accuracy and reliability of timekeeping, an RTC (Real-Time Clock) can be added Synchronizing the RTC with the GPS time would ensure accurate timekeeping. This setup would allow the RTC to maintain the correct time independently, and in cases where the RTC battery needs to be replaced, the time can be promptly reset by the GPS. With this improvement, the system would always know the current time, even when the GPS signal is weak.
- Hardware Optimization
Moving from development kits to a custom PCB design would be a significant improvement. Custom PCBs can be tailored to the specific needs of the telemetry system, reducing physical space requirements.

In conclusion, this project has achieved significant advances in the VRT telemetry system, meeting the objectives set and overcoming the technical challenges. The proposed future enhancements will build on this foundation to further improve performance and reliability for future races.

# 7 | Appendix

- Original project report
- Source code
- Configuration file example
- Test file

All the appendices are available in the git repository at the following link:

https://github.com/svankappel/Telemetry-for-the-Formula-Student

# Bibliography

[1] FS-Rules_2023_v1.1.pdf. URL: https : / / www . formulastudent . de / fileadmin/user_upload/all/2023/rules/FS- Rules_2023_v1. 1.pdf (https://www.formulastudent.de/fileadmin/user_upload/all/2023/rules/FS-Rules_2023_v1.1.pdf) (visited on 05/26/2023).
[2] Valais Wallis Racing Team. URL: https://www.vrt- fs.ch/ (https://www.vrt-fs.ch/) (visited on 05/26/2023).
[3] CAN Controller — Zephyr Project Documentation. URL: https : / / docs . zephyrproject.org/latest/hardware/peripherals/can/controller. html (https://docs.zephyrproject.org/latest/hardware/peripherals/can/controller.html) (visited on 03/01/2024).
[4] Workqueue Threads — Zephyr Project Documentation. URL: https://docs.zephyrproject.org/latest/kernel/services/threads/workqueue. html#work-item-lifecycle (https://docs.zephyrproject.org/latest/kernel/services/threads/workqueue.html#work-item-lifecycle) (visited on 07/26/2023).
[5] SiRF Technology Inc. “NMEA Reference Manual”. In: (2007). URL: https://www.sparkfun.com/datasheets/GPS/NMEA%20Reference%20Manual-Rev2.1-Dec07.pdf. (https://www.sparkfun.com/datasheets/GPS/NMEA%20Reference%20Manual-Rev2.1-Dec07.pdf)
[6] File Systems — Zephyr Project Documentation. URL: https://docs.zephyrproject.org/latest/services/file_system/index.html (https://docs.zephyrproject.org/latest/services/file_system/index.html) (visited on 07/28/2023).
[7] Universal Asynchronous Receiver-Transmitter (UART) — Zephyr Project Documentation. URL: https://docs.zephyrproject.org/latest/hardware/peripherals/uart.html (https://docs.zephyrproject.org/latest/hardware/peripherals/uart.html) (visited on 05/25/2024).

# Acronyms

BMS Battery Management System. 9

CAN Controller Area Network. 9, 13, 15, 16, 20, 27–29

CSV Comma-Separated Values. 6, 13, 18, 19

JSON JavaScript Object Notation. 6

QSPI Quad SPI. 9

SPI Serial Peripheral Interface. 9, 41

UART Universal Asynchronous Receiver Transmitter. 9, 10, 18, 24, 25, 29

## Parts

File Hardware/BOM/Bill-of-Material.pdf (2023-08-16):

Supplier | Nbr. | Supplier's Number | Manufacturer | Description | unit price | total price | ordered
Bill of Material - Telemetry System | | | | | Last update : 29.06.2023
Mouser | 9 | 80-C603C104K5RAC3121 | KEMET | Capacitor 1608 - 100 nF | 0,07 | 0,63 CHF | from stock
Mouser | 2 | 80-CBR06C220J5GAUTO | KEMET | Capacitor 1608 - 22 pF | 0,14 | 0,28 CHF | from stock
Mouser | 2 | 80-CBR06C101J5GAUTO | KEMET | Capacitor 1608 - 100 pF | 0,46 | 0,92 CHF | from stock
Mouser | 1 | 80-C0603X472K5GAUTO | KEMET | Capacitor 1608 - 4.7 nF | 0,40 | 0,40 CHF | from stock
Mouser | 1 | 810-C1005X7R1H103KBE | TDK | Capacitor 1005 - 10 nF | 0,14 | 0,14 CHF | from stock
Mouser | 1 | 810-C1005C0G1H470G | TDK | Capacitor 1005 - 47 pF | 0,35 | 0,35 CHF | from stock
Mouser | 2 | 80-C1206C106Z4VACTU | KEMET | Capacitor 3216 - 10 uF | 0,41 | 0,82 CHF | from stock
Mouser | 1 | 71-TNPW060310R0DEEA | Vishay | Resistor 1608 - 10 Ohm | 0,44 | 0,44 CHF | from stock
Mouser | 1 | 71-TNPW0603100KBEEA | Vishay | Resistor 1608 - 100 kOhm | 0,50 | 0,50 CHF | from stock
Mouser | 4 | 71-CRCW0603-120-E3 | Vishay | Resistor 1608 - 120 Ohm | 0,09 | 0,36 CHF | from stock
Mouser | 1 | 871-B82793C104N201 | EPCOS/TDK | Common mode choke | 2,07 | 2,07 CHF | 15.06.2023
Mouser | 1 | 495-TCK-141 | TRACO Power | EMC Choke | 6,23 | 6,23 CHF | 15.06.2023
Mouser | 1 | 994-0402DC-27NXGRW | Coilcraft | RF Inductor, Wirewound, 1005 - 27 nH | 1,41 | 1,41 CHF | 15.06.2023
Mouser | 1 | 581-CX3225SB16D0FLJ | Kyocera | Quartz 16 MHz | 1,17 | 1,17 CHF | 15.06.2023
Digikey | 1 | 497-13262-1-ND | STMicroelectronics | Automotive dual-line TVS diode | 0,41 | 0,41 CHF | 15.06.2023
Digikey | 1 | 296-23759-6-ND | Texas Instruments | 6 channels bidirectionnal level shifter | 1,50 | 1,50 CHF | 15.06.2023
Digikey | 2 | 296-21929-1-ND | Texas Instruments | 4 channels bidirectionnal level shifter | 1,03 | 2,06 CHF | 15.06.2023
Mouser | 1 | 781-SI1016X-T1-GE3 | Vishay | Complementary N- and P-Channel 20 V (D-S) MOSFET | 0,42 | 0,42 CHF | 15.06.2023
Mouser | 1 | 579-MCP2515-I/ML | Microchip | Stand-Alone CAN Controller with SPI Interface | 2,50 | 2,50 CHF | 15.06.2023
Mouser | 1 | 595-SN65HVD232D | Texas Instruments | CAN Interface IC 3.3-V CAN TRANSCEIVER | 2,97 | 2,97 CHF | 15.06.2023
Mouser | 1 | 495-TSR-1-2433 | TRACO Power | Non-Isolated DC/DC Converters 3.3v | 5,75 | 5,75 CHF | 15.06.2023
Mouser | 1 | 377-MAX-M10S-00B | Ublox | Standard precision GNSS module | 20,67 | 20,67 CHF | 15.06.2023
Mouser | 1 | 595-SN74LVC2G07DCKR | Texas Instruments | Buffers & Line Drivers Dual w/ Open-Drain | 0,43 | 0,43 CHF | 15.06.2023

Passive components

Integrated Circuits

Mouser | 1 | 538-22-05-7048 | Molex | Headers & Wire Housings 4C RA F/L HEADER | 1,17 | 1,17 CHF | from stock
Mouser | 1 | 538-22-27-2041 | Molex | Headers & Wire Housings 4 POS HEADER | 0,39 | 0,39 CHF | from stock
Mouser | 1 | 538-43045-0200 | Molex | Headers & Wire Housings 2 CKT R/A HEADER | 1,10 | 1,10 CHF | from stock
Mouser | 1 | 538-73251-1150 | Molex | SMA connector | 4,10 | 4,10 CHF | 15.06.2023
Mouser | 1 | 640-MEM20510019500A | GCT | Memory Card Connectors Micro SD | 1,12 | 1,12 CHF | 15.06.2023
Digikey | 2 | A132510-ND | TE Connectivity | CONN D-SUB PLUG 9POS R/A SLDR | 1,92 | 3,84 CHF | from stock
Digikey | 1 | 1568-1504-ND | Sparkfun | USB UART Serial breakout | 14,85 | 14,85 CHF | 15.06.2023
Mouser | 1 | 949-NRF7002-DK | Nordic Semi | nRF-7002 DK | 57,44 | 57,44 CHF | 02.06.2023
Mouser | 1 | 377-ANN-MB-00 | Ublox | Antennas Multi-band active GNSS antenna - SMA | 55,84 | 55,84 CHF | 15.06.2023
Digitec | 1 | 23079748 | Asus | Wifi Router - Asus RT-AX86U Pro | 247,00 | 247,00 CHF | 15.06.2023
Distrelec | 1 | 301-27-198 | EAO | Light button | 18,95 | 18,95 CHF | 29.06.2023
Distrelec | 1 | 302-20-253 | Taoglas | Dual Band wifi antenna | 15,64 | 15,64 CHF | 15.06.2023
Digikey | 1 | ADP-SMAM-RPSF-G-ND | Linx Technologies | SMA to RP-SMA adapter | 6,72 | 6,72 CHF | 15.06.2023
Distrelec | 1 | 301-31-595 | Nedis | Antenna cable SMA 2m | 10,29 | 10,29 CHF | 15.06.2023
Digikey | 1 | 490-4982-ND | Murata | Microwave Coaxial adapter | 27,70 | 27,70 CHF | 15.06.2023
Eurocircuit | 1 | - | Eurocircuit | 4 Layer PCB | 130,00 | 130,00 CHF | 15.06.2023

## 648,58 CHF

PCB

Miscellaneous

# Total :

Connectors

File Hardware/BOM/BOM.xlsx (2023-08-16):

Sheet: whole list
Supplier | Nbr. | Supplier's Number | Manufacturer | Description | unit price | total price | ordered
Bill of Material - Telemetry System |  |  |  |  | Last update : 29.06.2023
Passive components
Mouser | 9 | 80-C603C104K5RAC3121 | KEMET | Capacitor 1608 - 100 nF | 0.07 | 0.63 CHF | from stock
Mouser | 2 | 80-CBR06C220J5GAUTO | KEMET | Capacitor 1608 - 22 pF | 0.14 | 0.28 CHF | from stock
Mouser | 2 | 80-CBR06C101J5GAUTO | KEMET | Capacitor 1608 - 100 pF | 0.46 | 0.92 CHF | from stock
Mouser | 1 | 80-C0603X472K5GAUTO | KEMET | Capacitor 1608 - 4.7 nF | 0.40 | 0.40 CHF | from stock
Mouser | 1 | 810-C1005X7R1H103KBE | TDK | Capacitor 1005 - 10 nF | 0.14 | 0.14 CHF | from stock
Mouser | 1 | 810-C1005C0G1H470G | TDK | Capacitor 1005 - 47 pF | 0.35 | 0.35 CHF | from stock
Mouser | 2 | 80-C1206C106Z4VACTU | KEMET | Capacitor 3216 - 10 uF | 0.41 | 0.82 CHF | from stock
Mouser | 1 | 71-TNPW060310R0DEEA | Vishay | Resistor 1608 - 10 Ohm | 0.44 | 0.44 CHF | from stock
Mouser | 1 | 71-TNPW0603100KBEEA | Vishay | Resistor 1608 - 100 kOhm | 0.50 | 0.50 CHF | from stock
Mouser | 4 | 71-CRCW0603-120-E3 | Vishay | Resistor 1608 - 120 Ohm | 0.09 | 0.36 CHF | from stock
Mouser | 1 | 871-B82793C104N201 | EPCOS/TDK | Common mode choke | 2.07 | 2.07 CHF | 2023-06-15
Mouser | 1 | 495-TCK-141 | TRACO Power | EMC Choke | 6.23 | 6.23 CHF | 2023-06-15
Mouser | 1 | 994-0402DC-27NXGRW | Coilcraft | RF Inductor, Wirewound, 1005 - 27 nH | 1.41 | 1.41 CHF | 2023-06-15
Mouser | 1 | 581-CX3225SB16D0FLJ | Kyocera | Quartz 16 MHz | 1.17 | 1.17 CHF | 2023-06-15
Digikey | 1 | 497-13262-1-ND | STMicroelectronics | Automotive dual-line TVS diode | 0.41 | 0.41 CHF | 2023-06-15
Integrated Circuits
Digikey | 1 | 296-23759-6-ND | Texas Instruments | 6 channels bidirectionnal level shifter | 1.50 | 1.50 CHF | 2023-06-15
Digikey | 2 | 296-21929-1-ND | Texas Instruments | 4 channels bidirectionnal level shifter | 1.03 | 2.06 CHF | 2023-06-15
Mouser | 1 | 781-SI1016X-T1-GE3 | Vishay | Complementary N- and P-Channel 20 V (D-S) MOSFET | 0.42 | 0.42 CHF | 2023-06-15
Mouser | 1 | 579-MCP2515-I/ML | Microchip | Stand-Alone CAN Controller with SPI Interface | 2.50 | 2.50 CHF | 2023-06-15
Mouser | 1 | 595-SN65HVD232D | Texas Instruments | CAN Interface IC 3.3-V CAN TRANSCEIVER | 2.97 | 2.97 CHF | 2023-06-15
Mouser | 1 | 495-TSR-1-2433 | TRACO Power | Non-Isolated DC/DC Converters 3.3v | 5.75 | 5.75 CHF | 2023-06-15
Mouser | 1 | 377-MAX-M10S-00B | Ublox | Standard precision GNSS module | 20.67 | 20.67 CHF | 2023-06-15
Mouser | 1 | 595-SN74LVC2G07DCKR | Texas Instruments | Buffers & Line Drivers Dual w/ Open-Drain | 0.43 | 0.43 CHF | 2023-06-15
Connectors
Mouser | 1 | 538-22-05-7048 | Molex | Headers & Wire Housings 4C RA F/L HEADER | 1.17 | 1.17 CHF | from stock
Mouser | 1 | 538-22-27-2041 | Molex | Headers & Wire Housings 4 POS HEADER | 0.39 | 0.39 CHF | from stock
Mouser | 1 | 538-43045-0200 | Molex | Headers & Wire Housings 2 CKT R/A HEADER | 1.10 | 1.10 CHF | from stock
Mouser | 1 | 538-73251-1150 | Molex | SMA connector | 4.10 | 4.10 CHF | 2023-06-15
Mouser | 1 | 640-MEM20510019500A | GCT | Memory Card Connectors Micro SD | 1.12 | 1.12 CHF | 2023-06-15
Digikey | 2 | A132510-ND | TE Connectivity | CONN D-SUB PLUG 9POS R/A SLDR | 1.92 | 3.84 CHF | from stock
Miscellaneous
Digikey | 1 | 1568-1504-ND | Sparkfun | USB UART Serial breakout | 14.85 | 14.85 CHF | 2023-06-15
Mouser | 1 | 949-NRF7002-DK | Nordic Semi | nRF-7002 DK | 57.44 | 57.44 CHF | 2023-06-02
Mouser | 1 | 377-ANN-MB-00 | Ublox | Antennas Multi-band active GNSS antenna - SMA | 55.84 | 55.84 CHF | 2023-06-15
Digitec | 1 | 23079748 | Asus | Wifi Router - Asus RT-AX86U Pro | 247.00 | 247.00 CHF | 2023-06-15
Distrelec | 1 | 301-27-198 | EAO | Light button | 18.95 | 18.95 CHF | 2023-06-29
Distrelec | 1 | 302-20-253 | Taoglas | Dual Band wifi antenna | 15.64 | 15.64 CHF | 2023-06-15
Digikey | 1 | ADP-SMAM-RPSF-G-ND | Linx Technologies | SMA to RP-SMA adapter | 6.72 | 6.72 CHF | 2023-06-15
Distrelec | 1 | 301-31-595 | Nedis | Antenna cable SMA 2m | 10.29 | 10.29 CHF | 2023-06-15
Digikey | 1 | 490-4982-ND | Murata | Microwave Coaxial adapter | 27.70 | 27.70 CHF | 2023-06-15
PCB
Eurocircuit | 1 | - | Eurocircuit | 4 Layer PCB | 130.00 | 130.00 CHF | 2023-06-15
 |  |  |  | Total : |  | 648.58 CHF

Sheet: Altium BOM
NRF52DK socket | nRF53 development kit | B1 | 1 | nRF5340DK SOCKET
100n | Capacitor | C1, C2, C3, C8, C9, C10, C13, C16, C17 | 9 | CAPACITOR 1608 REFLOW
22pF | Capacitor | C4, C5 | 2 | CAPACITOR 1608 REFLOW
100pF | Capacitor | C6, C7 | 2 | CAPACITOR 1608 REFLOW
10uF | Capacitor | C11, C12 | 2 | CAPACITOR 3216 REFLOW
47pF | Capacitor | C14 | 1 | CAPACITOR 1608 REFLOW
10nF | Capacitor | C15 | 1 | CAPACITOR 1608 REFLOW
4.7nF | Capacitor | C18 | 1 | CAPACITOR 1608 REFLOW
ESDCAN__-2BLY | Automotive dual-line TVS diode | D1 | 1 | SOT23 P0.95 C1.6x3.0 H1.3
D-SUB 9 MALE GROUNDED | D-Subminiature 9 way Plug Right Angle | J1, J2 | 2 | D-SUB 9 MALE ANGLE
MOLEX 22057048 | KK 254 Wire-to-Board Header, Right-Angle, 4 Circuits | J3 | 1 | MOLEX 22057048
MOLEX 43045-0200 | Micro-Fit 3.0 Right-Angle Header, 3.00mm, Dual Row, 2 Circuits | J4 | 1 | MOLEX 43045-0200
732511150 | SMA EDGE Molex 732511150 | J5 | 1 | SMA EDGE Molex 732511150
MOLEX 22272041 | KK 254 Wire-to-Board Header, Vertical, 4 Circuits | J6 | 1 | MOLEX 22272041
GTC MEM20_1-00-195-00-A | SD Card Micro | J7 | 1 | SD MICRO GCT MEM2051-00-195-00-A
{Value} | JUMPER 3 POS | JP1, JP2, JP3 | 3 | JUMPER3 SMD 1608
 | Inductor Common Mode Filter | L1 | 1 | L CM 2X B82793C EPCOS
 | Inductor | L2 | 1 | TCK141
27nH | Inductor | L3 | 1 | INDUCTOR 1608 REFLOW
 | Screw Hex Socket Unconnected BN610 | Mec1, Mec2, Mec3, Mec4, Mec5, Mec6, Mec7 | 7 | Screw Hex Socket M3X5 Unconnected
10 | Resistor | R1 | 1 | RESISTOR 1608 REFLOW
100k | Resistor | R2 | 1 | RESISTOR 1608 REFLOW
120 | Resistor | R3, R4, R5, R6 | 4 | RESISTOR 1608 REFLOW
Si1016X | Complementary N- and P-Channel 20 V (D-S) MOSFET | T1 | 1 | SOT563F P0.5 C1.6x1.2 H0.6
TXB0106PWR | 6-Bit Bidirectional Level-Shifting and Voltage Translator With Auto-Direction Sensing and ±15-kV ESD Protection | U1 | 1 | TSSOP16 P0.65 C5.0x4.5 H1.1
MCP2515I/ML | Stand-Alone CAN Controller with SPI Interface | U2 | 1 | QFN20 P0.5 T2.05x2.05 C4.0x4.0 H0.85
SN65HVD232D | CAN Bus Transceiver 3V3 | U3 | 1 | SO8 P1.27 C4.0X5.0 H1.75
TXB0104PWR | 4-Bit Bidirectional Voltage-Level Translator With utomatic Direction Sensing and ±15-kV ESD Protection | U4, U7 | 2 | TSSOP14 P0.65 C4.4x5.0 H1.1
 | DC/DC Converter | U5 | 1 | TRACO TSR 1
SN74LVC2G17 | Dual Schmitt-Trigger Buffer | U6 | 1 | SOT23-6 P0.95 C1.5x3.0 H1.3
MAX-M10S-00B | Standard precision GNSS module | U8 | 1 | MAXM10S00B
 | Crystal C3.2x2.5 Kyocera CX3225SB | X1 | 1 | CRYSTAL C3.2x2.5 Kyocera CX3225SB

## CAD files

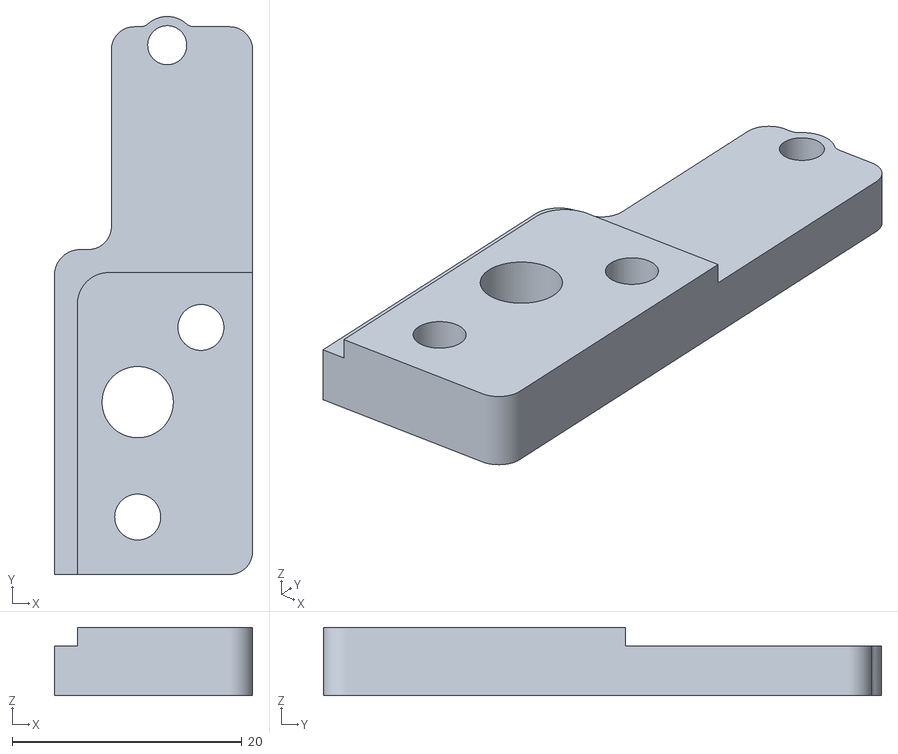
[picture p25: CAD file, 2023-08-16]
Hardware/AntennaConnectorHolder/bottom.stl
17.2 x 48.6 x 5.94

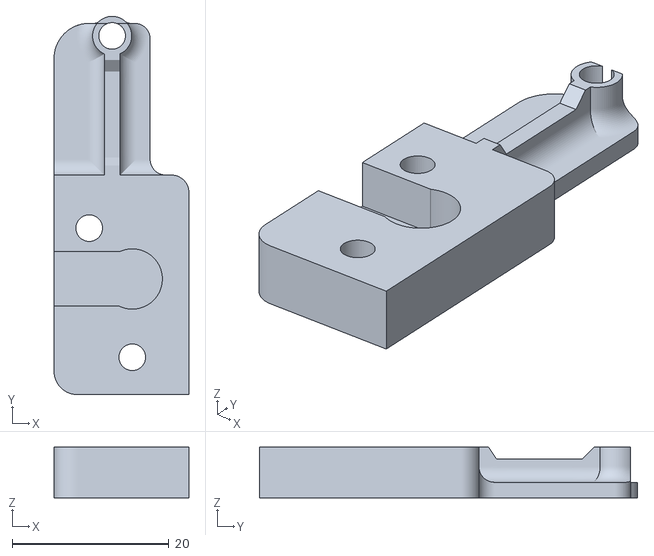
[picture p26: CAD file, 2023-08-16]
Hardware/AntennaConnectorHolder/top.stl
17.3 x 48.3 x 6.50

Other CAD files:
Hardware/AntennaConnectorHolder/connectorHolder.f3d

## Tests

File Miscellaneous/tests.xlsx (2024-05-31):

During Development Tests
System Parameters
Wifi | connected | connectd | connectd | connectd | connected | connected |  | connected | connected |  | connected | connected | connected |  | connected | connected | connected | connected | connected | connected | connected | connected | connected | connected | connected | connected | connected | connected | connected
Log recording | enabled | enabled | enabled | enabled | enabled | enabled |  | enabled | enabled |  | enabled | enabled | enabled |  | enabled | enabled | enabled | enabled | enabled | enabled | enabled | enabled | enabled | enabled | enabled | enabled | enabled | enabled | enabled
LogFrameRate [recording/sec] | 20 | 30 | 40 | 50 | 20 | 50 |  | 50 | 20 |  | 20 | 50 | 100 |  | 100 | 100 | 100 | 100 | 100 | 100 | 200 | 200 | 200 | 200 | 300 | 400 | 1000 | 1000 | 1000
Ignored CANBUS messages rate [message/sec] | 0 | 0 | 0 | 0 | 0 | 0 |  | 600 | 600 |  | 600 | 600 | 600 |  | 3000 | 2000 | 2000 | 1000 | 1000 | 1000 | 1000 | 1000 | 1000 | 0 | 0 | 0 | 0 | 1000 | 2000
CANBUS message rate [message/sec] | 200 | 200 | 200 | 200 | 300 | 300 |  | 100 | 100 |  | 100 | 200 | 300 |  | 800 | 1200 | 1600 | 2200 | 2800 | 3400 | 1600 | 2200 | 2800 | 3400 | 3400 | 3400 | 3400 | 0 | 1600
Cache flush | yes | yes | yes | yes | yes | yes |  | yes | yes |  | no | no | no |  | no | no | no | no | no | no | no | no | no | no | no | no | no | no | no
System works without failure | yes | yes | yes | yes | yes | no |  | no | no |  | yes | yes | no |  | yes | yes | yes | yes | yes | yes | yes | yes | yes | yes | yes | yes | yes | yes | yes
Test time [min] | 30 | 30 | 30 | 30 | 30 | - |  |  |  |  | 80 | 60 | - |  | 30 | 30 | 40 | 30 | 30 | 40 | 30 | 30 | 30 | 30 | 30 | 30 | 30 | 30 | 30
Failure : CAN buffer overflow after[min] | - | - | - | - | - | 35 |  | 2 | 7 |  | - |  | 28
System Features
can filter | no | no | no | no | no | no |  | yes | yes |  | yes | yes | yes |  | yes | yes | yes | yes | yes | yes | yes | yes | yes | yes | yes | yes | yes | no | no
Log recording and monitoring system splitted into two separated devices | no | no | no | no | no | no |  | no | no |  | no | no | no |  | yes | yes | yes | yes | yes | yes | yes | yes | yes | yes | yes | yes | yes | yes | yes
Characterization Tests on latest system release
 |  |  |  |  | Results |  | Base system |  |  | Upgrade on base hardware |  |  | New hardware |  | New hardware/nofilter
Measurement | Limit of functionning with the highest rates
Wifi | connected |  |  |  |  |  | lograte | canbus rate |  | lograte | canbus rate |  | lograte | canbus rate | lograte | canbus rate
GPS | active with fix |  |  |  |  |  | 50 | 1 |  | 100 | 1 |  | 1000 | 1 | 1000 | 2800
Log recording | enabled |  |  |  |  |  | 50 | 200 |  | 100 | 300 |  | 1000 | 1200 | 800 | 2900
Number of sensors | 22 |  |  |  |  |  | 20 | 300 |  | 50 | 500 |  | 1000 | 2200 | 500 | 3200
Number of different CAN messages destinated to the telemetry system | 8 |  |  |  |  |  | 10 | 350 |  | 20 | 700 |  | 1000 | 3400 | 200 | 3400
Number of different CAN messages not destinated to the telemetry system | 4 |  |  |  |  |  | 5 | 400 |  | 10 | 800 |  | 1 | 3400 | 1 | 3400
Test time | 30 minutes |  |  |  |  |  | 1 | 400 |  | 1 | 800 |  | 200 | 3400
Failure criteria | can buffer overflow |  |  |  |  |  |  |  |  |  |  |  | 500 | 3400
Measurement |  |  |  |  |  |  |  |  |  |  |  |  | 1000 | 3400
Can max message rate | 3400 [message/sec]
log recording maximum rate | 1000 [records / sec]
Base system tests | only messages destinated to the telemetry system
Upgrade on base system + new hardware tests + new hardware without filter | can bus is filled to 3400 msg/sec with other messages not destinated to the telemetry (not included in the measurements)

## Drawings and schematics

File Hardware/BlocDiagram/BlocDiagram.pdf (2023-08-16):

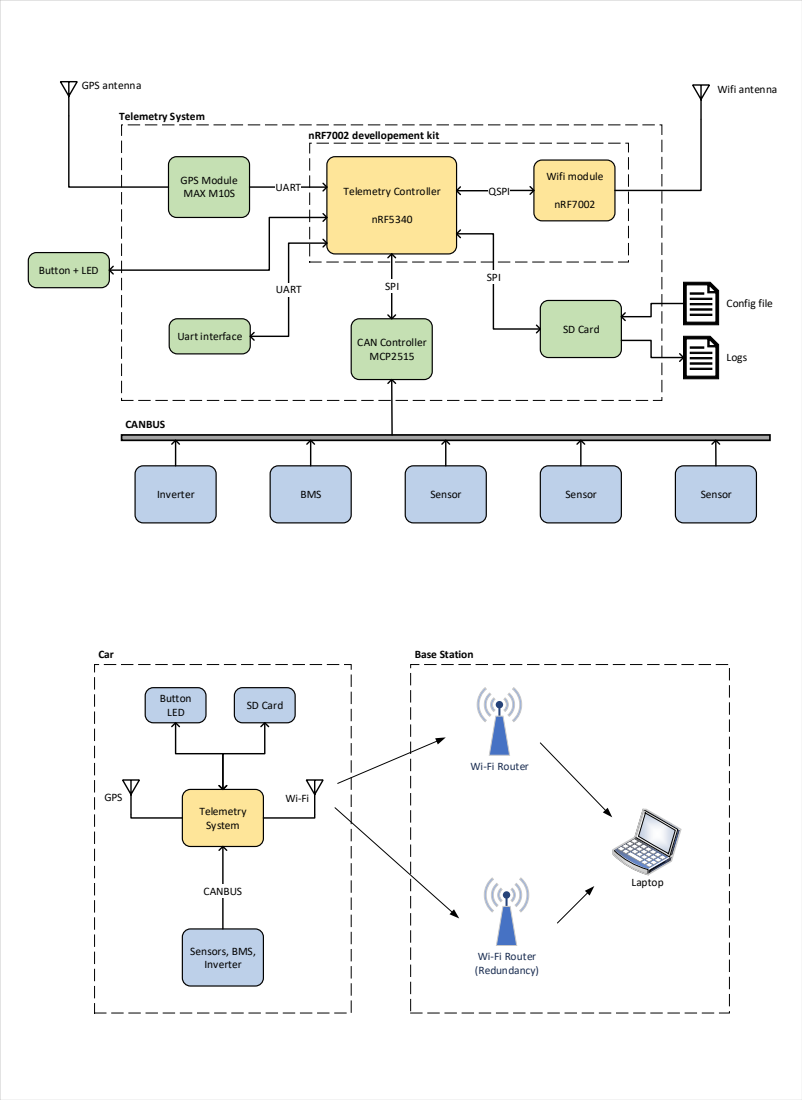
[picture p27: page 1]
Telemetry Controller; nRF5340; Wifi module; nRF7002; QSPI; CAN Controller MCP2515; SD Card; SPI; Wifi antenna; Config file; Logs; Telemetry System; CANBUS; Inverter; BMS; Sensor; GPS Module; MAX M10S; UART; GPS antenna; Uart interface; nRF7002 devellopement kit; Laptop; Base Station; Sensors, BMS, Inverter; Car; Button + LED; GPS

SD Card Button
LED

Wi-Fi Router

(Redundancy)

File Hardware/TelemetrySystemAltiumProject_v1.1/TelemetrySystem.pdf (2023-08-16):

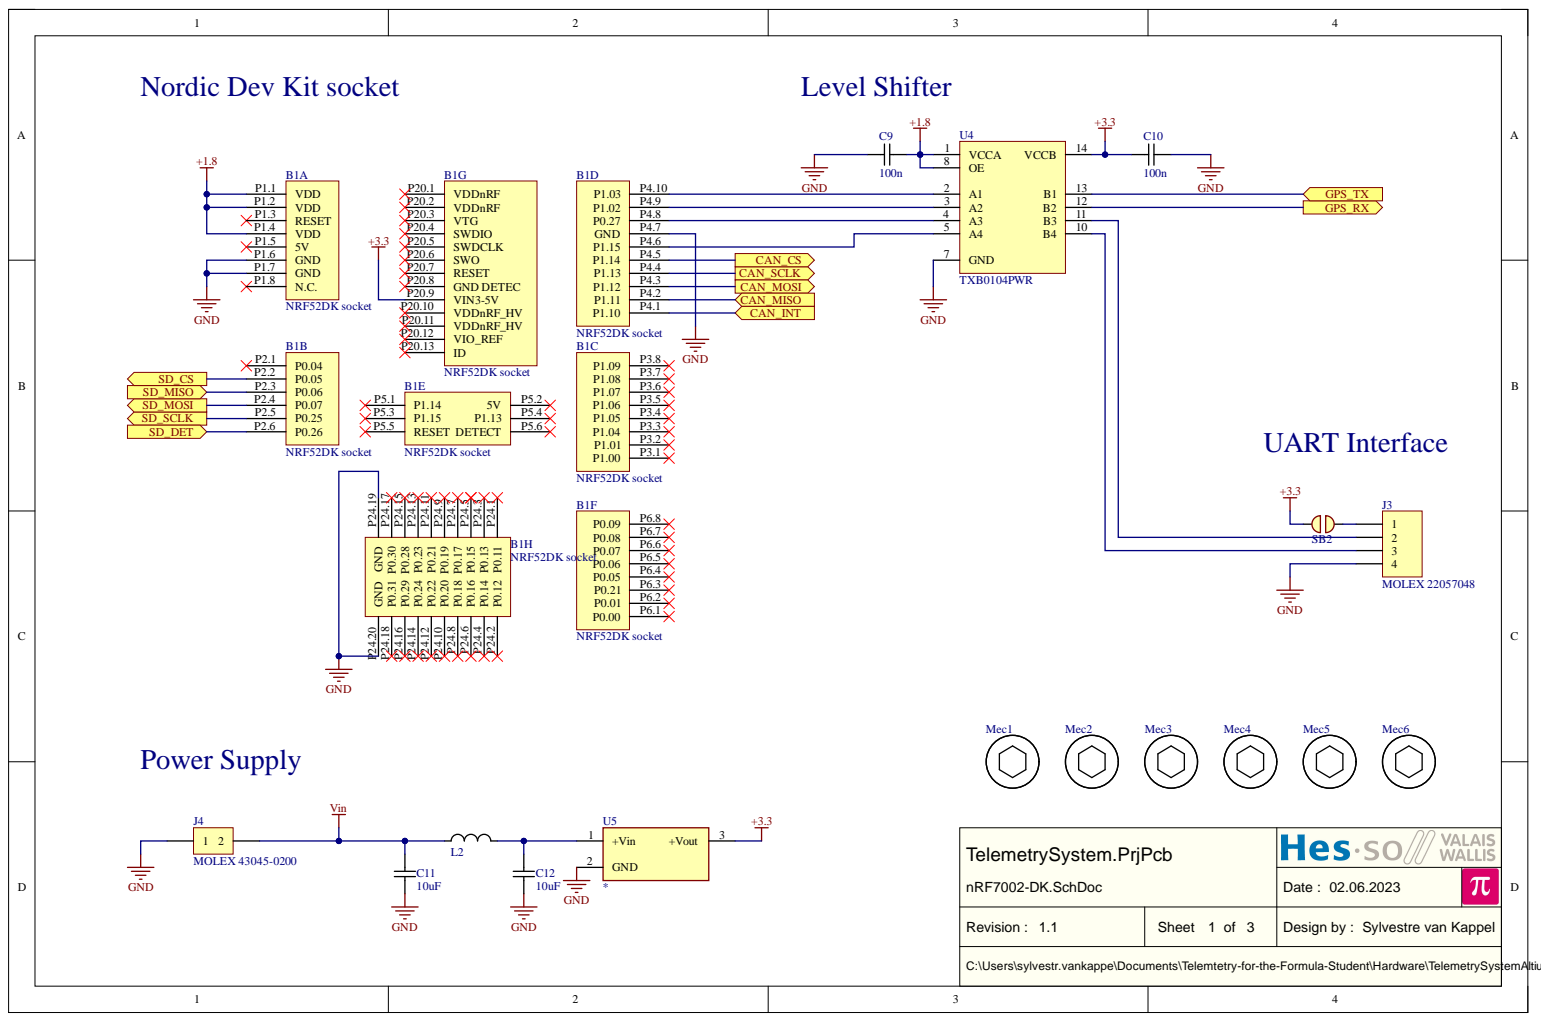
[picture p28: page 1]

Date : 02.06.2023

Revision : 1.1 | Sheet 1 of 3 | Design by : Sylvestre van Kappel

C:\Users\sylvestr.vankappe\Documents\Telemtetry-for-the-Formula-Student\Hardware\TelemetrySystemAltiumProject_v1.1\nRF7002-DK.SchDoc

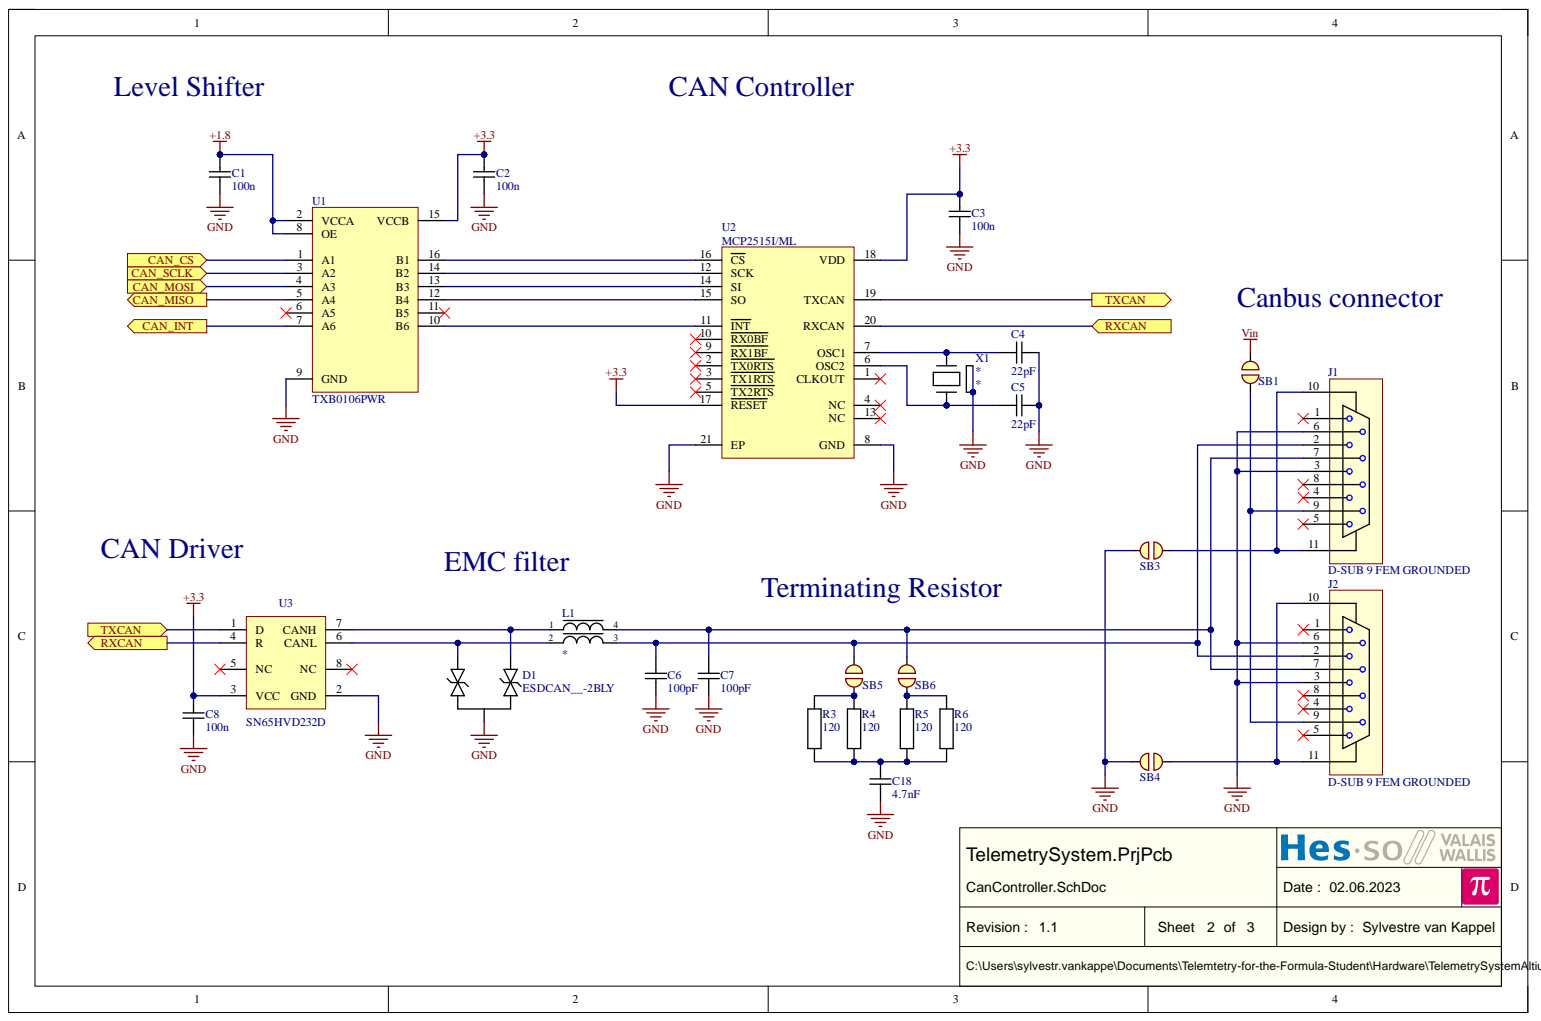
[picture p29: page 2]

TelemetrySy stem.Prj P c b CanController.SchDoc

Date : 02.06.2023

Revision : 1.1 | Sheet 2 of 3 | Design by : Sylvestre van Kappel

tetry-for-the-Formula-Student
Telem

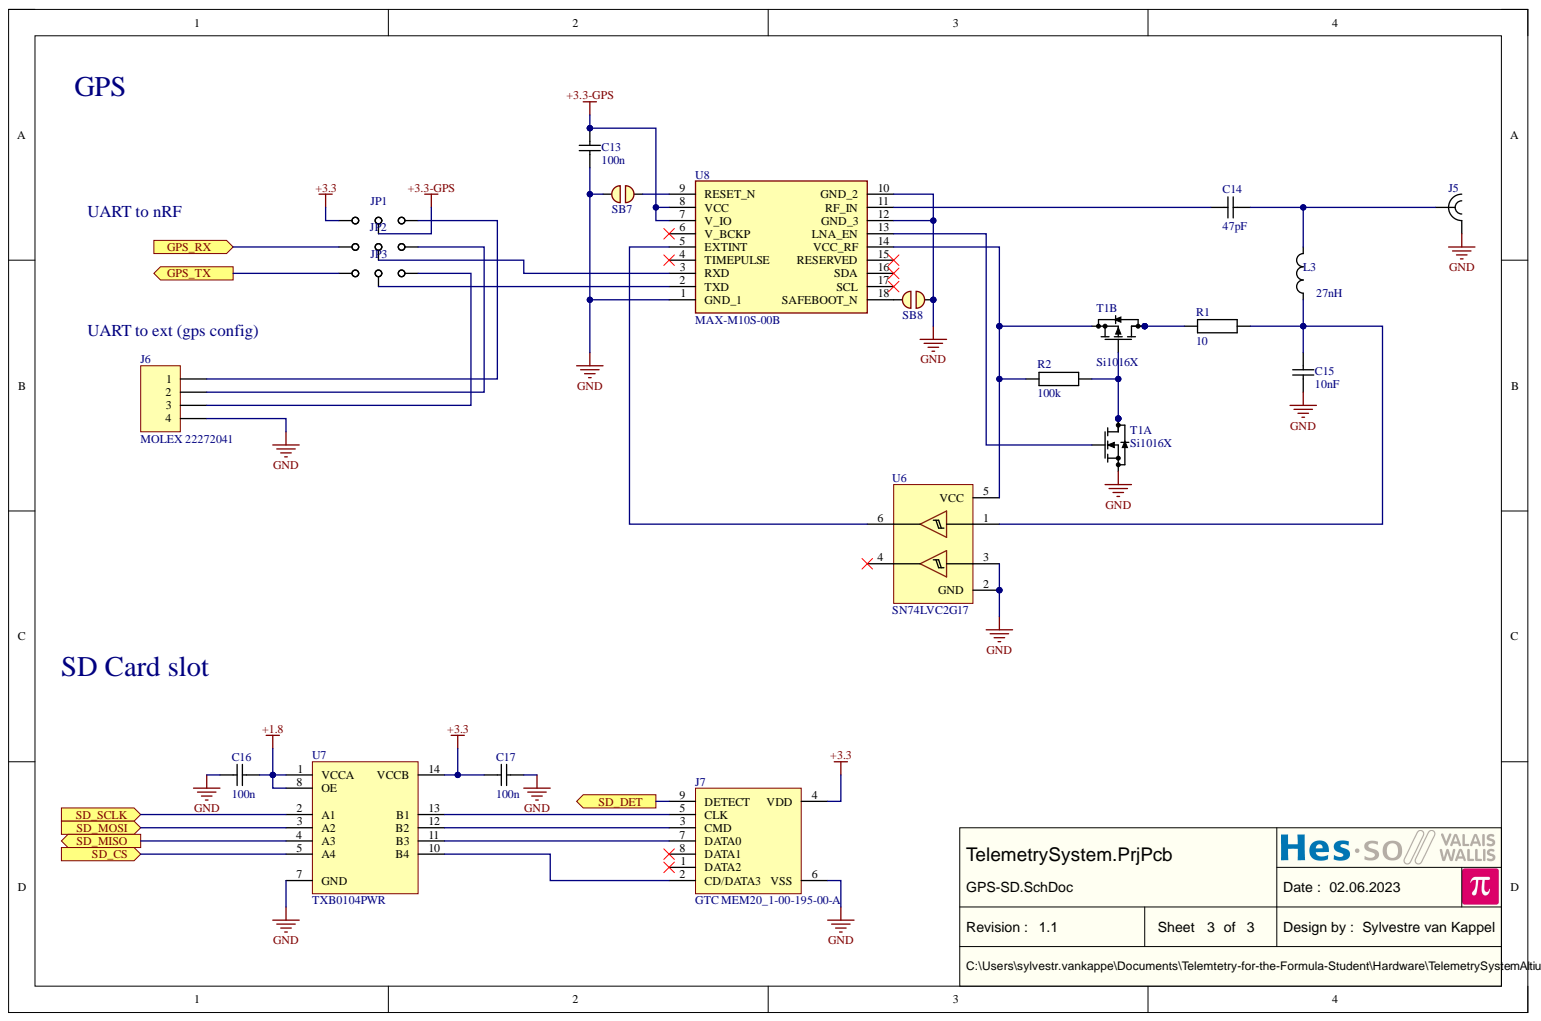
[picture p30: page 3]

UART to ext (gps config)

C:\Users\sylvestr.vankappe\Documents\Telemtetry-for-the-Formula-Student\Hardware\TelemetrySystemAltiumProject_v1.1\GPS-SD.SchDoc

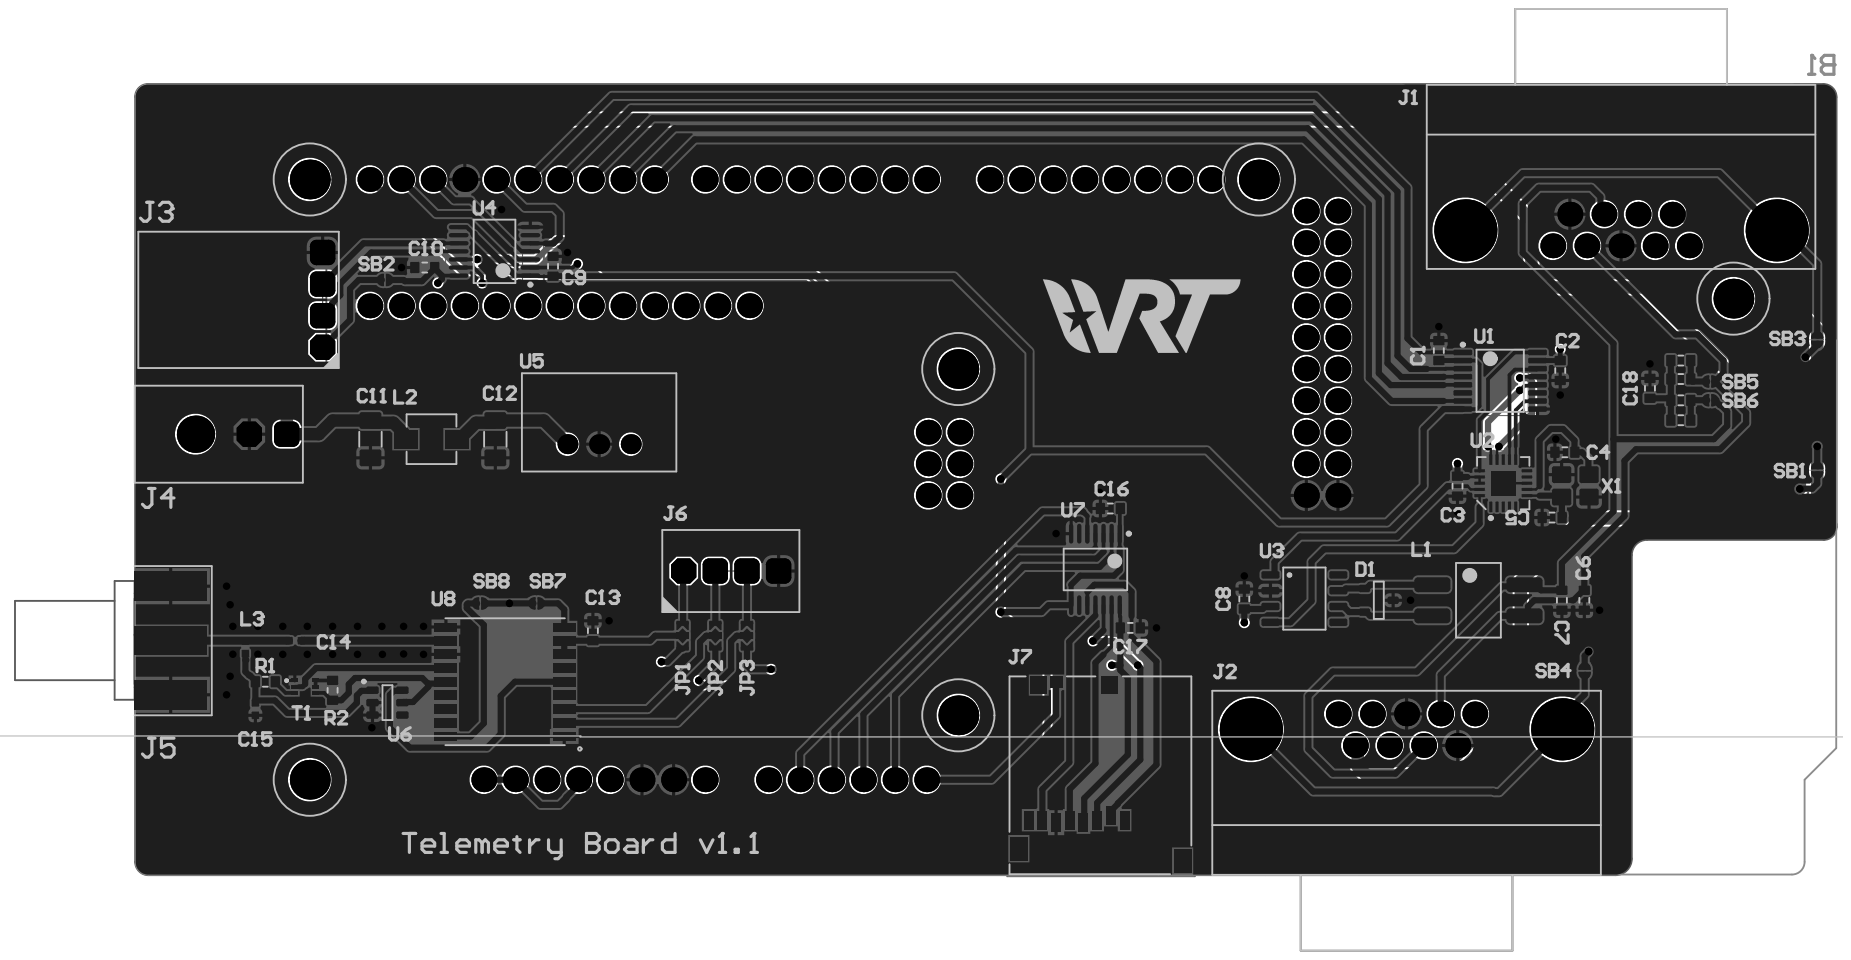
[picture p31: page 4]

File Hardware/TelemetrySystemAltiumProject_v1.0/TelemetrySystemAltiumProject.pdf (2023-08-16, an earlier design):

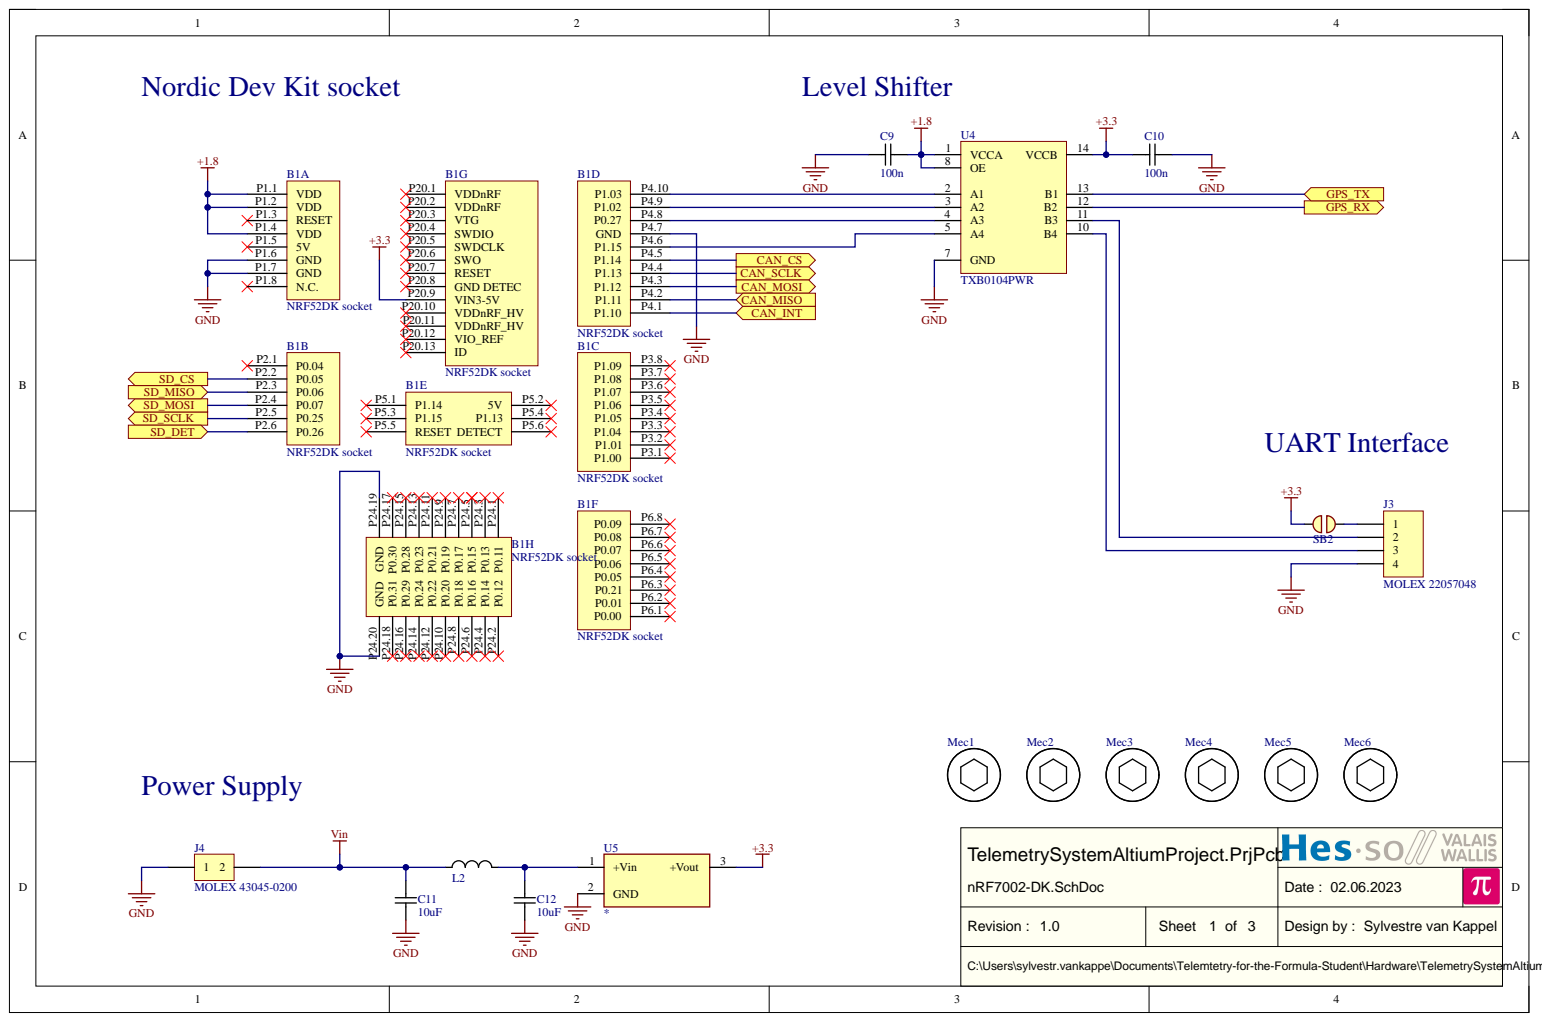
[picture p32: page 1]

TelemetrySystemAltiumProject.PrjPcb nRF7002-DK.SchDoc

Revision : 1.0 | Sheet 1 of 3 | Design by : Sylvestre van Kappel

C:\Users\sylvestr.vankappe\Documents\Telemtetry-for-the-Formula-Student\Hardware\TelemetrySystemAltiumProject\nRF7002-DK.SchDoc

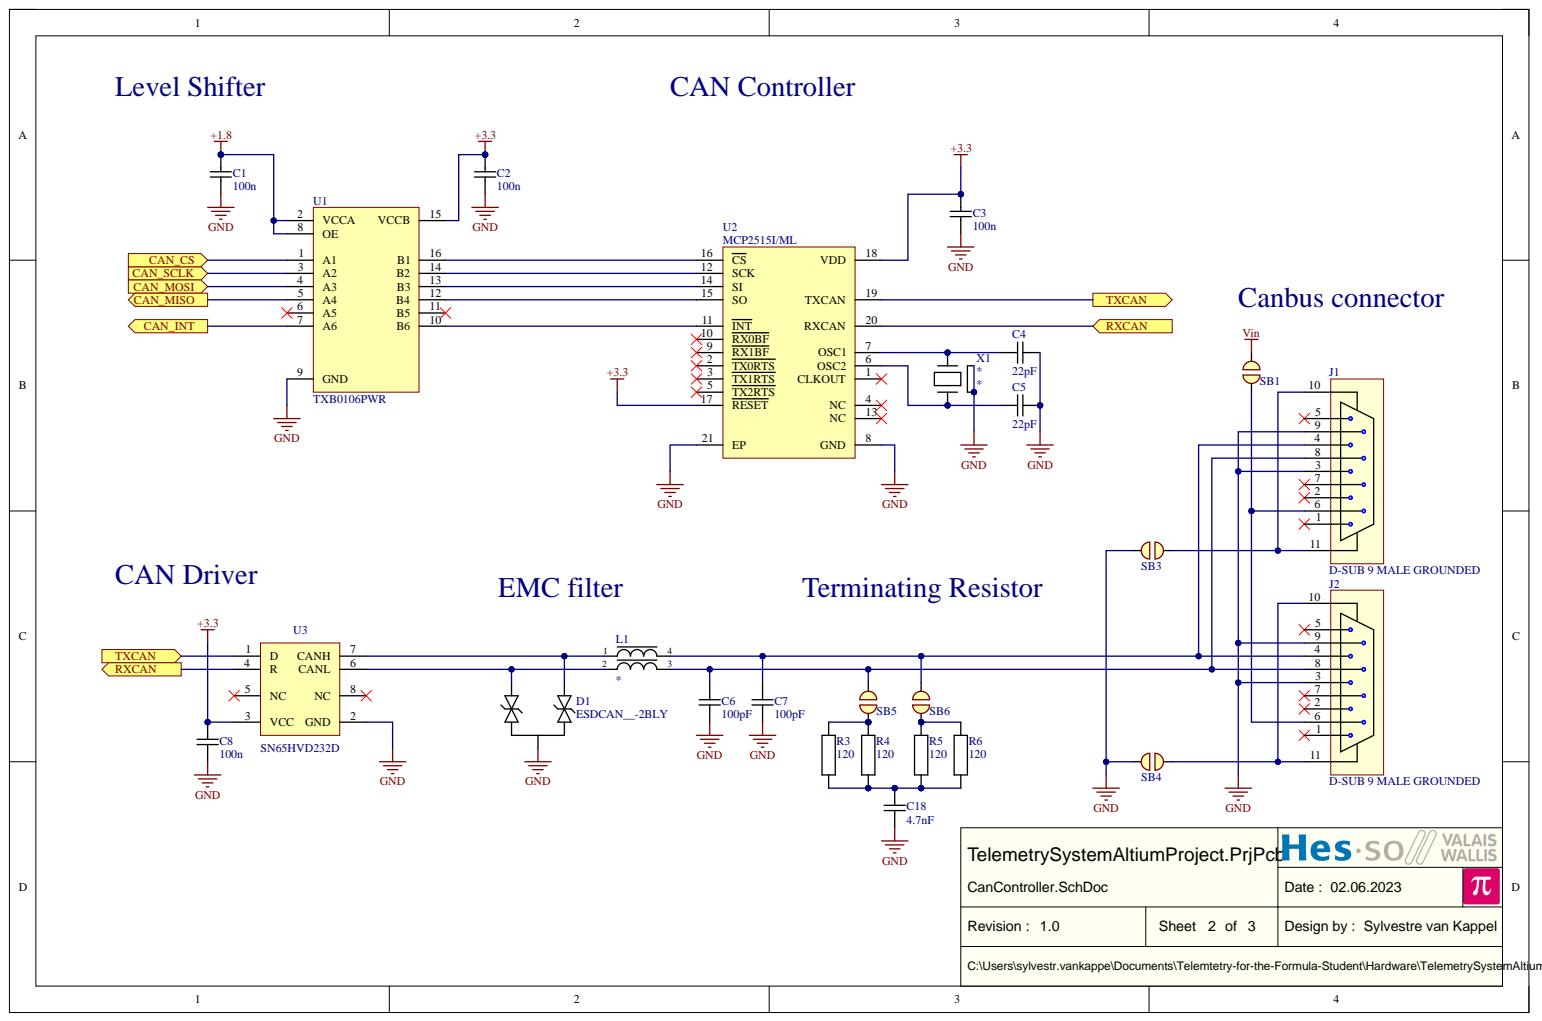
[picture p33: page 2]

TelemetrySystemAltiumProject.PrjPcb CanController.Sch D o c

Date : 02.06.202 3

Revision : 1.0 | Sheet 2 of 3 | Design by : Sylvestre van Kappel

C:\Users\sylvestr.vankappe\Documents\Telemtetry-for-the-Formula-Student\Hardware\TelemetrySystemAltiumProject\CanContro

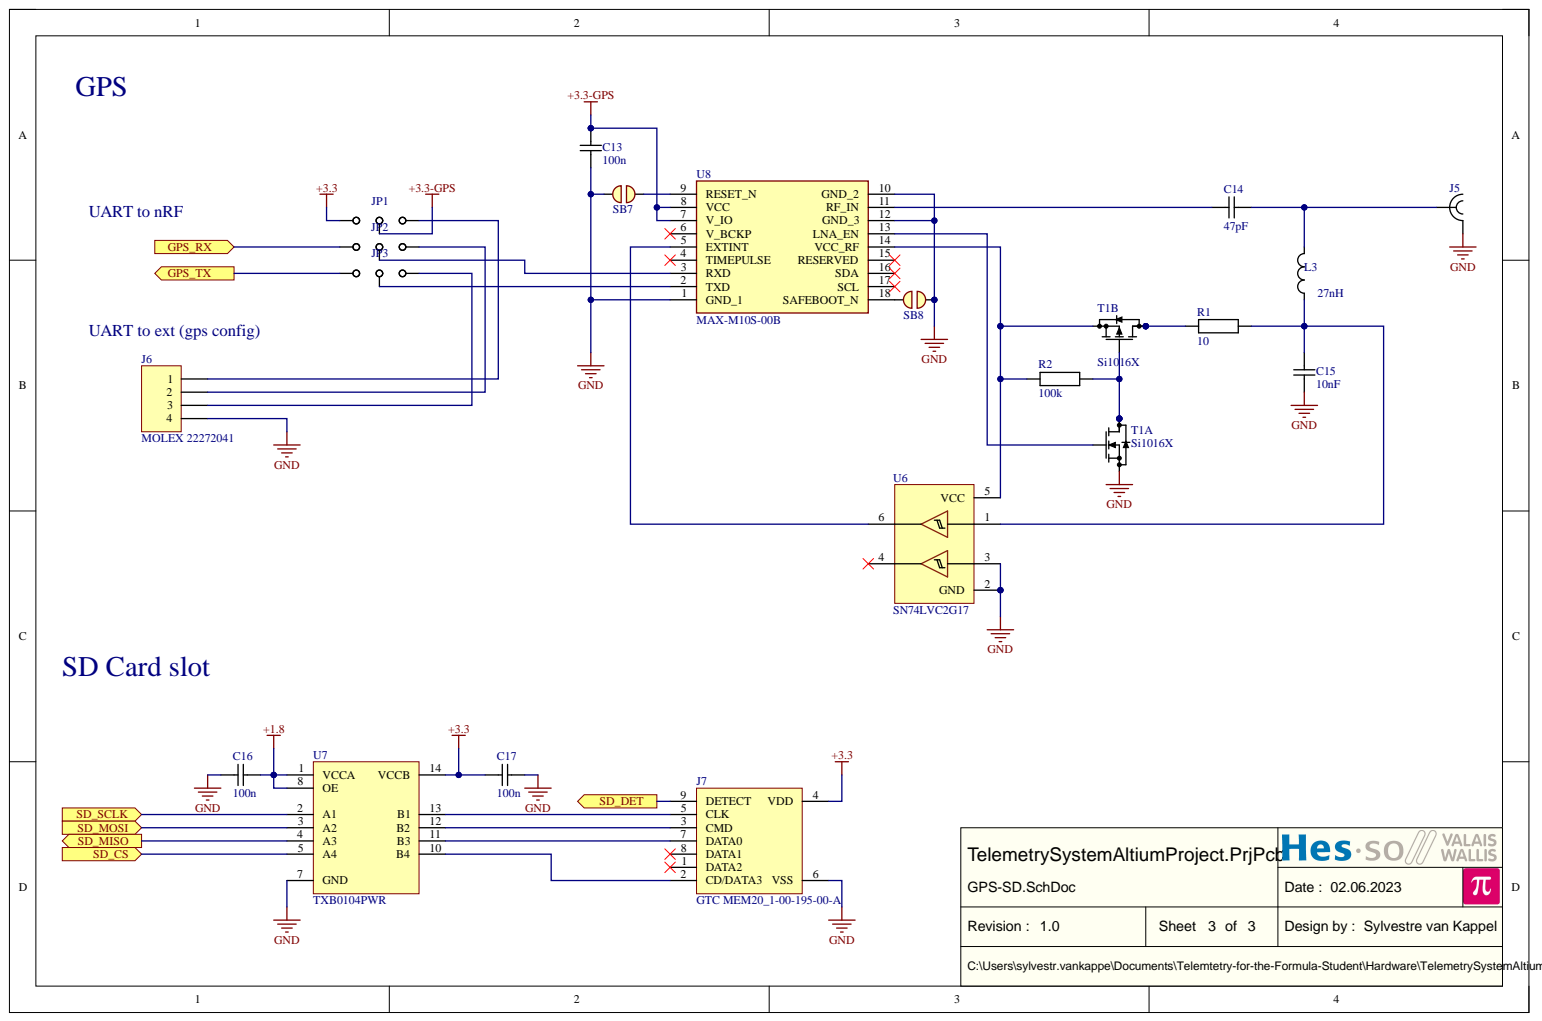
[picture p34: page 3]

UART to ext (gps config)

A4 5 | DATA1 8
GND 7 | DATA2 1

C:\Users\sylvestr.vankappe\Documents\Telemtetry-for-the-Formula-Student\Hardware\TelemetrySystemAltiumProject\GPS-SD.SchDoc

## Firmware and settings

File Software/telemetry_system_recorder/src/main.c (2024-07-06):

/*! --------------------------------------------------------------------
 *	Telemetry System	-	@file main.c
 *----------------------------------------------------------------------
 * HES-SO Valais Wallis 
 * Systems Engineering
 * Infotronics
 * ---------------------------------------------------------------------
 * @author Sylvestre van Kappel
 * @date 02.08.2023
 * ---------------------------------------------------------------------
 * @brief Main of Telemetry system. Starts all tasks of the program
 * ---------------------------------------------------------------------
 * Telemetry system for the Valais Wallis Racing Team.
 * This file contains code for the onboard device of the telemetry
 * system. The system receives the data from the sensors on the CAN bus 
 * and the data from the GPS on a UART port. An SD Card contains a 
 * configuration file with all the system parameters. The measurements 
 * are sent via Wi-Fi to a computer on the base station. The measurements 
 * are also saved in a CSV file on the SD card. 
 *--------------------------------------------------------------------*/


//includes
#include <zephyr/kernel.h>
#include <nrfx_clock.h>

// include all tasks files
//#include "task/wifi_sta.h"
//#include "task/udp_client.h"
#include "task/led.h"
//#include "task/data_sender.h"
#include "task/data_logger.h"
#include "task/memory_management.h"
#include "task/config_read.h"
#include "task/button_manager.h"
#include "task/can_controller.h"
//#include "task/gps_controller.h"


//--------------------------------------------------------------------------
//			main
int main(void)
{

	/* 128MHz clock*/
	nrfx_clock_divider_set(NRF_CLOCK_DOMAIN_HFCLK,NRF_CLOCK_HFCLK_DIV_1);
	printk("Starting %s with CPU frequency: %d MHz\n", CONFIG_BOARD, SystemCoreClock/MHZ(1));


	Task_Led_Init();				//start led controller Thread
	
	Task_Button_Manager_Init();		//start button manager

	int ret = read_config();		//read configuration file

	if(ret == 0)			//configuration file ok
	{
		Task_Data_Logger_Init();		//start data logger

		Task_CAN_Controller_Init();		//start can controller thread

		k_sleep(K_SECONDS(7));
		if(configFile.RecordOnStart)                            //if record autostart is selected
        	data_Logger_button_handler_start();
	}

	k_sleep( K_FOREVER );
	return 0;
}

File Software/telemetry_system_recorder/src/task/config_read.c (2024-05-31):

/*! --------------------------------------------------------------------
 *	Telemetry System	-	@file config_read.c
 *----------------------------------------------------------------------
 * HES-SO Valais Wallis 
 * Systems Engineering
 * Infotronics
 * ---------------------------------------------------------------------
 * @author Sylvestre van Kappel
 * @date 02.08.2023
 * ---------------------------------------------------------------------
 * @brief reads the configuration file on the SD card
 * ---------------------------------------------------------------------
 * Telemetry system for the Valais Wallis Racing Team.
 * This file contains code for the onboard device of the telemetry
 * system. The system receives the data from the sensors on the CAN bus 
 * and the data from the GPS on a UART port. An SD Card contains a 
 * configuration file with all the system parameters. The measurements 
 * are sent via Wi-Fi to a computer on the base station. The measurements 
 * are also saved in a CSV file on the SD card. 
 *--------------------------------------------------------------------*/

//includes
#include <zephyr/logging/log.h>
LOG_MODULE_REGISTER(config, 4);
#include <zephyr/kernel.h>
#include <errno.h>
#include <stdio.h>
#include <zephyr/device.h>
#include <zephyr/storage/disk_access.h>
#include <zephyr/data/json.h>
#include <zephyr/fs/fs.h>
#include <ff.h>
#include <stdlib.h>
#include <zephyr/toolchain.h>
#include <string.h>

#include <zephyr/init.h>
#include <zephyr/drivers/gpio.h>
#include <zephyr/sys/util.h>
#include <zephyr/drivers/uart.h>

//include project files
#include "config_read.h"
#include "memory_management.h"

//file system
static FATFS fat_fs;

// SD mounting info 
static struct fs_mount_t mp = {
	.type = FS_FATFS,
	.fs_data = &fat_fs,
};

// SD mount name
static const char *disk_mount_pt = "/SD:";

//json config file struct
struct config configFile;
bool configOK;		//boolean variable for printing state on led
static uint8_t sd_card_buffer[512];


// uart node
#define UART_DEVICE_NODE_CONFIG DT_CHOSEN(zephyr_shell_uart_config)
static const struct device *const uart_dev_config = DEVICE_DT_GET(UART_DEVICE_NODE_CONFIG);
struct Data{
	uint8_t * readBufPointer;
	uint16_t size;
};
void serial_cb_config(const struct device *dev, struct Data * userData);
bool sendFinished = false;

//struct for Wifi router data description
static const struct json_obj_descr wifi_router_descr[] = {
	JSON_OBJ_DESCR_PRIM(struct sWiFiRouter, SSID, JSON_TOK_STRING),
	JSON_OBJ_DESCR_PRIM(struct sWiFiRouter, Password, JSON_TOK_STRING)
};

//struct for redundancy Wifi router data description
static const struct json_obj_descr wifi_router_red_descr[] = {
	JSON_OBJ_DESCR_PRIM(struct sWiFiRouterRedundancy, SSID, JSON_TOK_STRING),
	JSON_OBJ_DESCR_PRIM(struct sWiFiRouterRedundancy, Password, JSON_TOK_STRING),
	JSON_OBJ_DESCR_PRIM(struct sWiFiRouterRedundancy, Enabled, JSON_TOK_TRUE)
};

//struct for udp servers description
static const struct json_obj_descr server_descr[] = {
	JSON_OBJ_DESCR_PRIM(struct sServer, address, JSON_TOK_STRING),
	JSON_OBJ_DESCR_PRIM(struct sServer, port, JSON_TOK_NUMBER)
};

//struct for GPS data description
static const struct json_obj_descr gpsdata_descr[] = {
	JSON_OBJ_DESCR_PRIM(struct sGPSData, NameLive, JSON_TOK_STRING),
	JSON_OBJ_DESCR_PRIM(struct sGPSData, NameLog, JSON_TOK_STRING),
	JSON_OBJ_DESCR_PRIM(struct sGPSData, LiveEnable, JSON_TOK_TRUE),
};

//struct for CAN filter description
static const struct json_obj_descr canfilter_descr[] = {
	JSON_OBJ_DESCR_PRIM(struct sCANFilter, id, JSON_TOK_STRING),
	JSON_OBJ_DESCR_PRIM(struct sCANFilter, mask, JSON_TOK_STRING)
};

//struct for CAN button data description
static const struct json_obj_descr canbuttondata_descr[] = {
	JSON_OBJ_DESCR_PRIM(struct sCANButtonData, CanID, JSON_TOK_STRING),
	JSON_OBJ_DESCR_PRIM(struct sCANButtonData, index, JSON_TOK_NUMBER),
	JSON_OBJ_DESCR_PRIM(struct sCANButtonData, match, JSON_TOK_STRING),
	JSON_OBJ_DESCR_PRIM(struct sCANButtonData, mask, JSON_TOK_STRING),
	JSON_OBJ_DESCR_PRIM(struct sCANButtonData, dlc, JSON_TOK_NUMBER)
};

//struct for CAN button description
static const struct json_obj_descr canbutton_descr[] = {
	JSON_OBJ_DESCR_OBJECT(struct sCANButton, StartLog, canbuttondata_descr),
  	JSON_OBJ_DESCR_OBJECT(struct sCANButton, StopLog, canbuttondata_descr)
};

//struct for CAN Led description
static const struct json_obj_descr canled_descr[] = {
	JSON_OBJ_DESCR_PRIM(struct sCANLed, CanID, JSON_TOK_STRING)
};

//struct for GPS CAN ids description
static const struct json_obj_descr canids_descr[] = {
	JSON_OBJ_DESCR_PRIM(struct sGPSCanIds, Lat, JSON_TOK_STRING),
	JSON_OBJ_DESCR_PRIM(struct sGPSCanIds, Long, JSON_TOK_STRING),
	JSON_OBJ_DESCR_PRIM(struct sGPSCanIds, TimeFixSpeed, JSON_TOK_STRING)
};
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

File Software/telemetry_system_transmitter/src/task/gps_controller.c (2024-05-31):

/*! --------------------------------------------------------------------
 *	Telemetry System	-	@file gps_controller.c
 *----------------------------------------------------------------------
 * HES-SO Valais Wallis 
 * Systems Engineering
 * Infotronics
 * ---------------------------------------------------------------------
 * @author Sylvestre van Kappel
 * @date 02.08.2023
 * ---------------------------------------------------------------------
 * @brief GPS Controller task receives data from the GPS module on the
 * 		  uart port and fill the GPS buffer with the received data
 * ---------------------------------------------------------------------
 * Telemetry system for the Valais Wallis Racing Team.
 * This file contains code for the onboard device of the telemetry
 * system. The system receives the data from the sensors on the CAN bus 
 * and the data from the GPS on a UART port. An SD Card contains a 
 * configuration file with all the system parameters. The measurements 
 * are sent via Wi-Fi to a computer on the base station. The measurements 
 * are also saved in a CSV file on the SD card. 
 *--------------------------------------------------------------------*/

//includes
#include <zephyr/logging/log.h>
LOG_MODULE_REGISTER(gps);
#include <zephyr/kernel.h>
#include <zephyr/init.h>
#include <zephyr/drivers/gpio.h>
#include <zephyr/device.h>
#include <zephyr/sys/util.h>
#include <zephyr/drivers/uart.h>
#include <stdlib.h>
#include <zephyr/toolchain.h>
#include <string.h>

//project file includes
#include "gps_controller.h"
#include "memory_management.h"
#include "config_read.h"


//! GPS thread priority level
#define GPS_CONTROLLER_STACK_SIZE 4096
//! GPS thread priority level
#define GPS_CONTROLLER_PRIORITY 2

//! GPS stack definition
K_THREAD_STACK_DEFINE(GPS_CONTROLLER_STACK, GPS_CONTROLLER_STACK_SIZE);
//! Variable to identify the GPS thread
static struct k_thread gpsControllerThread;

// uart node
#define UART_DEVICE_NODE_GPS DT_CHOSEN(zephyr_shell_uart_gps)

//max size of NMEA message
#define MSG_SIZE 85


tGps gpsBuffer;
K_MUTEX_DEFINE(gpsBufferMutex);

// queue to store up to 10 messages (aligned to 4-byte boundary) 
K_MSGQ_DEFINE(uart_msgq, MSG_SIZE, 10, 4);

//uart device declaration
static const struct device *const uart_dev_gps = DEVICE_DT_GET(UART_DEVICE_NODE_GPS);

// receive buffer used in UART ISR callback 
static char rx_buf[MSG_SIZE];
static int rx_buf_pos;

//serial callback function prototype
/*!
 * @brief Read characters from UART until line end is detected. Afterwards push the
 * 		  data to the message queue.
 */
void serial_cb(const struct device *dev, void *user_data);


//-----------------------------------------------------------------------------------------------------------------------
/*! GPS_Controller implements the GPS_Controller task
* @brief GPS_Controller read the UART form GPS and fill the sensorBuffer array 
*        
*/
void GPS_Controller(void)
{
	//gps fix
	bool gpsFix = false;
	
	//rx buffer
	char rx_buf[MSG_SIZE];

	//check if uart device is ready
	if (!device_is_ready(uart_dev_gps)) 
	{
		LOG_INF("UART device not found!");
		return;
	}
	// configure interrupt and callback to receive data 
	uart_irq_callback_user_data_set(uart_dev_gps, serial_cb, NULL);
	uart_irq_rx_enable(uart_dev_gps);

	// indefinitely wait for input from UART
	while (k_msgq_get(&uart_msgq, &rx_buf, K_FOREVER) == 0) 
	{

		//-----------------------------------------------------
		//		NMEA GSA Frame -	GPS receiver operating mod

		if(strstr(rx_buf,"$GNGSA"))
		{
			if(rx_buf[10]=='3')		//detect if gps has fix
				gpsFix=true;

			else
				gpsFix=false;

			k_mutex_lock(&gpsBufferMutex,K_FOREVER);		//lock gps buffer mutex
			gpsBuffer.fix = gpsFix;							//copy gps fix value to buffer
			k_mutex_unlock(&gpsBufferMutex);				//unlock mutex
		}

		//-----------------------------------------------------
		//	NMEA RMC Frame - contains time and date

		//different parsing because the frame could contain empty items
		// $GNRMC,162134.00,A,4617.63609,N,00731.94398,E,0.006,,170524,,,A,V*10

		if(strstr(rx_buf,"$GNRMC"))
		{
			// time and date buffers
			char utcHour[3];
			char utcMin[3];
			char utcSec[3];
			char cday[3];
			char cmonth[3];
			char cyear[3];
			
			char * ptr = rx_buf;

			char * timePtr;
			char * datePtr;

			int i = 0;		//loop index

			while(i<9)
			{
				if(*ptr==',')
				{
					i++;
					if(i==1)
					{
						timePtr = ptr+1;
					}
					if(i==9)
					{
						datePtr = ptr+1;
					}
				}
				ptr++;
			}

			strncpy(utcHour,timePtr,2);				// utc time
			utcHour[2] = '\0';
			strncpy(utcMin,timePtr+2,2);
			utcMin[2] = '\0';
			strncpy(utcSec,timePtr+4,2);
			utcSec[2] = '\0';

			strncpy(cyear,datePtr,2);				// date
			cyear[2] = '\0';
			strncpy(cmonth,datePtr+2,2);
			cmonth[2] = '\0';
			strncpy(cday,datePtr+4,2);
			cday[2] = '\0';
			
			//calculate values
			uint8_t hour = atoi(utcHour)+2;		//+2 to match center europa time
			uint8_t min = atoi(utcMin);
			uint8_t sec = atoi(utcSec);
			
			uint8_t day = atoi(cday);
			uint8_t month = atoi(cmonth);
			uint8_t year = atoi(cyear);

			k_mutex_lock(&gpsBufferMutex,K_FOREVER);		//lock gps buffer mutex
			gpsBuffer.hour=hour;
			gpsBuffer.min=min;
			gpsBuffer.sec=sec;
			gpsBuffer.day=day;
			gpsBuffer.month=month;
			gpsBuffer.year=year;
			k_mutex_unlock(&gpsBufferMutex);				//unlock mutex
		}
	

		//analyse other frames only if GPS is fixed
		if(gpsFix)	
		{
			//-----------------------------------------------------
			//	NMEA GLL Frame - contains latitude and longitude

			if(strstr(rx_buf,"$GNGLL"))
			{
				// NMEA frame DMm + sign
				char latDeg[4];
				char latMin[12];
				char latSign[2];
				char lonDeg[4];
				char lonMin[12];
				char lonSign[2];
				
				char * saveptr=NULL;			//strtok save pointer
				char * str = rx_buf;			//string of frame
				char * token = (char*)strtok_r(str,",",&saveptr);	// get first token

				int i = 0;		//loop index
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

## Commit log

2023-05-15 TB Start
    [planning.xlsx]
2023-05-15 update planning
    [planning.xlsx]
2023-05-15 sensor list
2023-05-15 test commit
    [composants.xlsx]
2023-05-26 Transmission study
    [composants.xlsx, planning.xlsx]
2023-05-30 transmission process report
    [composants.xlsx, planning.xlsx]
2023-05-30 Altium project created
    [TelemetryBoard.PrjPcb, TelemtryBoard_v1.0.PcbDoc, TelemtryBoard_v1.0.SchDoc]
2023-05-31 schematics start
    [BOM.xlsx, CanController.SchDoc, Debug.SchDoc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]
2023-06-01 nrf5340 schematics start
    [BOM.xlsx, CanController.SchDoc, Controller.SchDoc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]
2023-06-02 start shield dev
    [BOM.xlsx, CanController.SchDoc, Controller.SchDoc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]
2023-06-02 SDCard Schematics
    [BOM.xlsx, Controller.SchDoc, Debug.SchDoc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]
2023-06-06 GPS schematics finished + canbus module start
    [BOM.xlsx, CanController.SchDoc, Controller.SchDoc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]
2023-06-07 schematics finished (except gps)
    [BOM.xlsx, CanController.SchDoc, Controller.SchDoc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]
2023-06-07 PCB start
    [CanController.SchDoc, GPS-SD.SchDoc, TelemetryBoard.PcbDoc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]
2023-06-09 schematic finished (except gps)
    [CanController.SchDoc, GPS-SD.SchDoc, TelemetryBoard.PcbDoc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]
2023-06-09 altium project migrated to 4L
    [BOM.xlsx, CanController.SchDoc, Eurocircuits4L.PcbDoc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]
2023-06-12 Schematics ok+ rooting ok except gnd and vcc
    [CanController.SchDoc, Eurocircuits4L.PcbDoc, GPS-SD.SchDoc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]
2023-06-12 rooting finished
    [CanController.SchDoc, TelemetryBoard.PcbDoc, TelemetrySystemAltiumProject.PrjPcb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]
2023-06-13 BOM + cutout on pcb
    [BOM.xlsx, GPS-SD.SchDoc, Orders.xlsx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]
2023-06-14 pcb adapted + BOM completed
    [BOM.xlsx, TelemetryBoard.PcbDoc]
2023-06-14 présentation start + màj planning
    [planning.xlsx]
2023-06-15 BOM update (inductore wirewound + RF in 1005)
    [BOM.xlsx, Orders.xlsx]
2023-06-15 PCB update (gps RF validated by A. Andersson)
    [GPS-SD.SchDoc]
2023-06-16 report - intro
    [planning.xlsx]
2023-06-19 table des matières supprimée
2023-06-19 PCB ordered
    [TelemetryBoard.GBL, TelemetryBoard.GBO, TelemetryBoard.GBP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]
2023-06-19 PCB v1.0
    [TelemetryBoard.GBL, TelemetryBoard.GBO, TelemetryBoard.GBP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]
2023-06-19 folder cleaned
    [planning.xlsx]
2023-06-20 blinky thread
2023-06-21 wifi connection in thread
2023-06-22 udp server + client (not working9
    [main.c]
2023-06-23 Led control in separated thread
2023-06-26 udp multi socket (raw)
2023-06-29 report + sensor file update
    [data.csv]
2023-06-29 Export pdf + bloc diagram update
    [CanController.SchDoc, GPS-SD.SchDoc, TelemetrySystemAltiumProject.PrjPcb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]
2023-06-29 BOM update
    [BOM.xlsx]
2023-06-30 added sensors in config file
2023-06-30 data sender on sensor buffer with config file names
2023-07-03 data Sender in timer
2023-07-03 button manager + led control
2023-07-03 led code cleaned
2023-07-07 Frame Rate in config file
2023-07-09 socketCount rename
2023-07-10 mutex on sensor Buffer
2023-07-11 Can controller thread created
2023-07-11 reboot on SD card inserted
    [button_manager.c, main.c]
2023-07-11 button manager cleaned
2023-07-11 can tests (not working)
    [main.c]
2023-07-13 gps uart rx
2023-07-14 GPS read all frames + gps config
2023-07-17 Altium project v1.1
    [CanController.SchDoc, GPS-SD.SchDoc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]
2023-07-19 testbench - BMS
2023-07-19 testbench - tires
2023-07-25 Button manager ok
2023-08-07 connector holder
    [bottom.stl, connectorHolder.f3d, top.stl]
2023-08-14 update BOM + bloc diagram
    [BOM.xlsx]
2023-08-15 update BOM
    [BOM.xlsx]
2023-08-16 folder clean
    [planning.xlsx]
2023-08-16 clean altium folders
    [TelemetryBoard.GBL, TelemetryBoard.GBO, TelemetryBoard.GBP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]
2023-08-19 poster + pitch 4K
2024-03-01 test monitoring
    [tests.xlsx]
2024-03-01 configurable filter
    [tests.xlsx]
2024-03-08 button on CAN implemented
    [tests.xlsx]
2024-03-15 update config file for button on can
2024-03-15 can button working
2024-03-15 update config file for led
2024-03-15 led on the can working
2024-04-10 folder update
    [tests.xlsx]
2024-04-19 overlay files of both devices updated
2024-05-03 transfer done (problem at recorder with special char)
    [config_read.c]
2024-05-06 config file read new item for can IDS (not working)
    [config_read.c, main.c]
2024-05-13 transmit time fix speed
    [gps_controller.c]
2024-05-17 receive date and time (problem with wifi)
    [gps_controller.c, main.c]
2024-05-18 datalogger update (not working)
    [gps_controller.c]
2024-05-20 GPS Data transfer working (problem with recording stop)
    [config_read.c]
2024-05-25 test + diagrams
    [tests.xlsx]
2024-05-29 new diagram + chart of tests
    [tests.xlsx]
2024-05-31 update tests
    [tests.xlsx]
2024-06-04 buxfix : CAN button message match and mask
2024-07-06 Added more memory allocation in the stacks for bigger json and more sensors
